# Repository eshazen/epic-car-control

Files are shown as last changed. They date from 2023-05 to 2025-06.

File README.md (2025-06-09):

# epic-car-control

Arduino-based model car control for EPIC.  This is a PCB which mounts
on a model car used in the Partner Classes taught at EPIC.

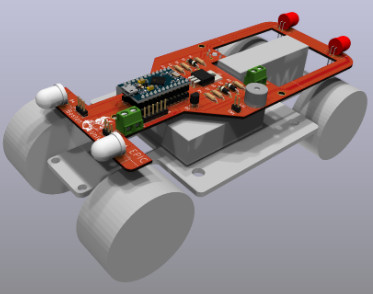
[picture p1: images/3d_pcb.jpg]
car


* [Electronics Talk](https://docs.google.com/presentation/d/1JKn2IykLU-F7YahLROMGz_joYOWPTk3rvR12y0UCeqs/edit?usp=drive_link) -- Google doc link for summer 2023 talk
* [Software Development Log](SoftwareLog.md)
* [Wiring Diagram](Slides/wiring_diagram.pdf) -- how to wire the PCB to the car
* [Programming Instructions](Slides/car_program.pdf) -- instructions to change the target distance

## Hardware features

* Arduino pro micro socket
* MOSFET for motor control
* Optical sensor for wheel revolution counter
* Headlights and taillights with individual control
* Small speaker
* Bottom-mounted pushbutton switch for user inputs
* Screw terminal connectors for a 6V battery pack (4xAA) and motor
* Header connector for a power switch

## Software

Current software in `Arduino/car_control/car_control.ino`

```
power-up reads distance set from EEPROM
   long (error) beep means invalid setting (default to 5)
Idle mode
   short press - drive for programmed distance
   long press - move to 10's set mode
10's set mode
   short press: add 10 revs
   long press: to 1's set mode
1's set mode
   short press: add 1 revs
   long press: save setting and exit to IDLE
```

Current setting displayed in binary on LEDs as

| Location | Value |
|:---|:---|
| Right Front | 1 |
| Left Front  | 2 |
| Left Rear | 4 |
| Right Rear  | 8 |

(value is sum of lit LEDs, or zero if all off)

Note that the current setting can be displayed with:

* **Long Press** - display 10's
* **Long Press** - display 1's
* **Long Press** - return to idle

Sensor test:

* Hold button while powering up
* Then press the button repeatedly:
  * first press: long beep, take reading, display low 4 bits
  * second press: display high 4 bits

Power down and up to exit test mode

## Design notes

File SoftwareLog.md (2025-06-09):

# Software log

**2025-06-08** Version 10

Another attempt to fix the EEPROM code.  Seems ok.
Programmed (40) boards for 2025 class.

**2025-06-03** Version 9

Still buggy EEPROM code

**2024-06-01** Version 8

Update sensor calibration values to 16 bit but bugs in EEPROM save so
doesn't restore correctly on power-up.

**2023-06-30** Working on sensor calibration

Created version 7.  Preliminary calibration mode.  Collects minimum
and maximum sensor readings and a threshold midway between them,
which is stored in EEPROM locations (2, 3).

Activate re-calibration by holding button down on power-up (replaces readout mode,
for now).  Spin front wheel until beeping stops.  Press button once
to go to normal driving mode.

A few other tweaks:  Ignore rotation sensor until running at speed.
I think it works well enough now.

**2023-06-29** First class

Deployed version 5.  All worked well on about half of the cars, but
the sensors didn't work well on the others.

**2023-06-19** Continuing on software.

The ISR stuff seems like a lot of work.  The debounce demo seems to
work fine with 20ms interrupts, so a main loop running at that speed
via delay() should be OK.  Here's the algo from the demo:

> Switch Debouncing uses high frequency hardware timer 50Hz == 20ms) to
> measure the time from the SW is pressed, debouncing time is 100ms =>
> SW is considered pressed if timer count is > 5, then call / flag SW is
> pressed When the SW is released, timer will count (debounce) until
> more than 50ms until consider SW is released.  We can set to flag or
> call a function whenever SW is pressed more than certain predetermined
> time, even before SW is released.

OK, first version is working ok.  Long/short button presses and rev
counter implemented using update() functions expected to be called
every ~20ms from loop().

**2023-06-18** Starting on working software.

Installed Arduino 2.1.0 as Appimage from the web.

`tone()` function works for beeping, and runs in background.

Idea:  use timer interrupts to record time/length of last button press.

Installing
[TimerInterrupt](https://github.com/khoih-prog/TimerInterrupt) v1.8.0
by Khoi Hoang, which claims to support the Leonardo.

This works OK but fights with tone(); Trying to create a unified ISR
which handles both, but the one with the button debounce demo seems to
take more than 1ms to run.

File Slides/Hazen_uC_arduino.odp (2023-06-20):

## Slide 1

EPIC Partner Class -- 2013

Soldering

and

Arduinos

## Soldering

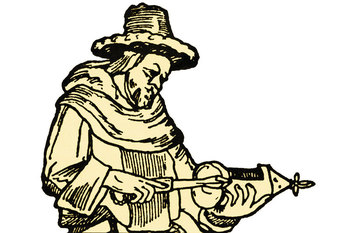
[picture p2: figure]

- Soldering is the joining of metal objects together. A filler metal (“solder”) is melted and flowed into the joint.
- Soldering was practiced in ancient Egypt at least 5000 years ago
- Soldering is used to attach electronic components to a board, and also for jewelery and other applications

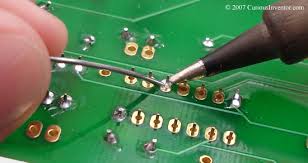
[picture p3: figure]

## Soldering Safety

- The iron gets hot! Don't burn yourself. Careful not to splash solder
- Solder is made of lead, which is poisonous Wash your hands when you are done; don't eat or drink while soldering
- Snipped component leads fly at high speeds Close your eyes or cover with your hands

## What's an Arduino?

A: A tiny computer

The black thing with all the legs

is a tiny computer called

a microcontroller

They can be programmed

in C or C++

They are used in lots of

things around your house

(microwave, stereo, TV...)

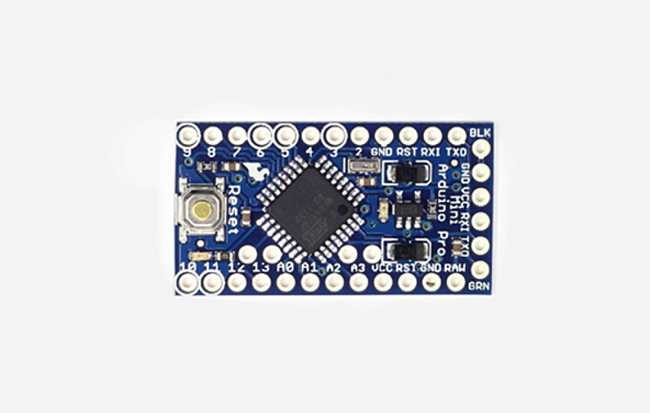
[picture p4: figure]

## Micro-what?

- Q: What exactly is a microcontroller (uC)? A: Just a very small (usually single-chip) computer
- Q: What features must a microcontroller have? A: A central processing unit (CPU) Program memory (usually flash) Data memory (at least registers, usually RAM too) Some input / output
- Q: What other features may a uC have? A: Counter/timer units, serial ports, A/D and D/A converters, plus sometimes special features such as USB, WiFi, light dimmers....

## Essential uC Components

Program Memory

Instructions (code)

Registers

(temporary storage)

Central

Processing

Unit

Input/

Output

External

Devices

Data Memory

(variables)

## Arduino “Sketch” Example It's almost exactly “C”, but...

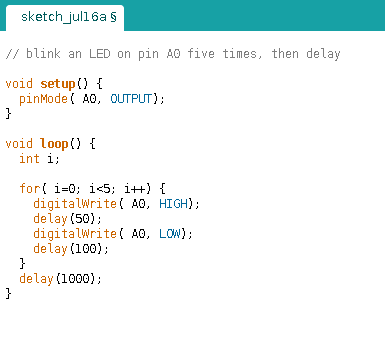
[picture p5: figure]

No “#includes” unless you use

a special library

Special function setup()
called once when program starts

pinMode() tells the Arduino
whether a pin is for input
our output

Special function loop()
called forever after setup()

DigitalWrite() sets a pin to
a specific “logic level”:
HIGH = 5V
LOW = 0V

No “printf” since there is no

keyboard / screen attached!

Special function delay()
stops the program for specified
number of milli-seconds
(1/1000 second steps)

## Circuit Example

Power supply

(two AA batteries)

Micro-

controller

LED

(output device)

resistor to limit

LED current

push-button

(input device)

## More about Input and Output

- Two types of devices:
  - Digital
    - On / Off only (like an LED or push-button)
    - Sometimes used in groups (i.e. for a keypad)
    - Can form a bus (special group with data and control) for example to control an LCD display
  - Analog
    - Variable level/speed (like a knob or a motor)
    - For input, use an ADC (analog-to-digital converter)
    - For output, use a DAC (digital-to-analog converter)
    - Often used for things like ultrasonic range finders, light sensors or speed control of motors

## Programming considerations

- Just like programming a “real computer”, except:
  - Generally C/C++ is the only language choice
  - Program memory is small! Programs must be short
  - Data memory is small! Only a few variables
  - Often there is no keyboard or display, so functions like printf() are not useful
  - Floating point math is “expensive” so best use only integers
  - For efficiency, pick variables of the right size (use a char if 8 bits is enough)

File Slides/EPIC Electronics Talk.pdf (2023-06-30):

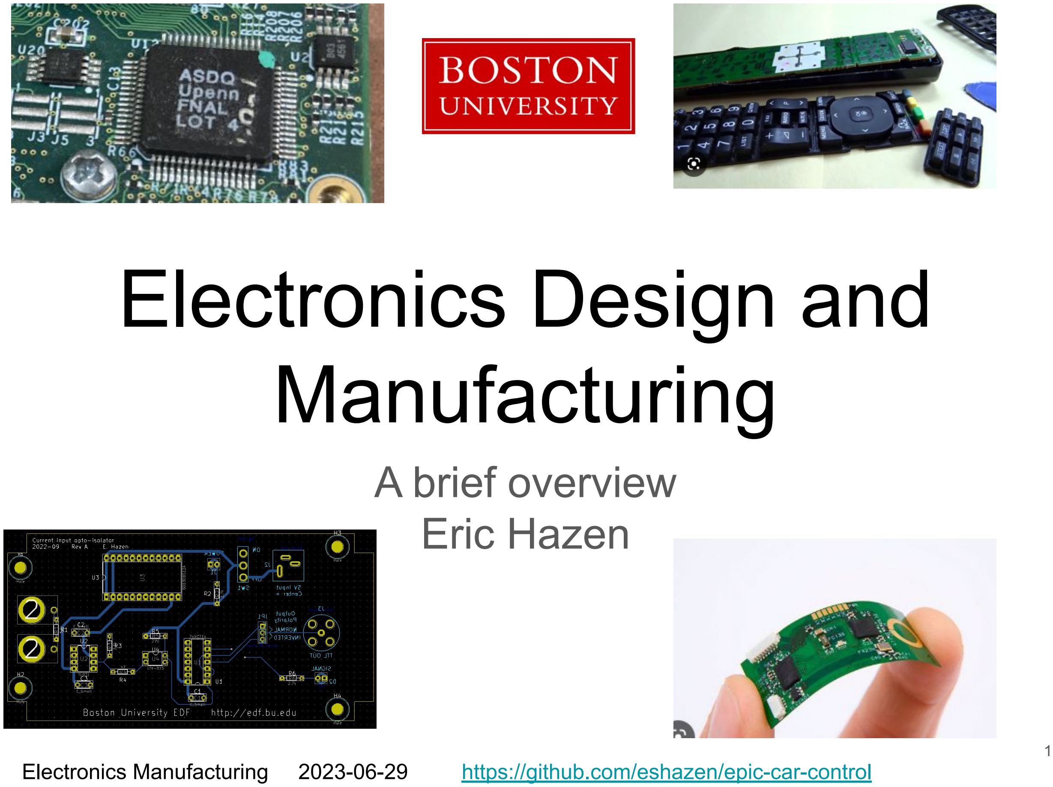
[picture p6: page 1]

# Electronics Design and Manufacturing

# A brief overview Eric Hazen

Electronics Manufacturing | 2023-06-29 | https://github.com/eshazen/epic-car-control

# About me…

Electronics Manufacturing | 2023-06-29 | E. Hazen | https://github.com/eshazen/epic-car-control

Professionally, I lead a team which built electronics for the CERN experiments which discovered the Higgs Boson
edf.bu.edu
(now retired)

In my spare time, I build
retro-electronics
(tube amps, calculators,
clocks…)

…and I fly planes and drive my Miata!

# Outline

## - Electronic Component types

## - Design Case Study

## - Packaging Considerations

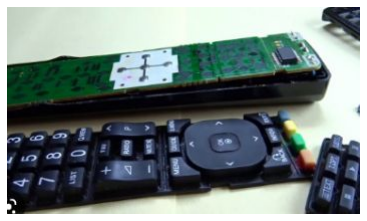
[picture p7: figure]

## - Power and Cooling

## - Summary

# Introduction to electronic components

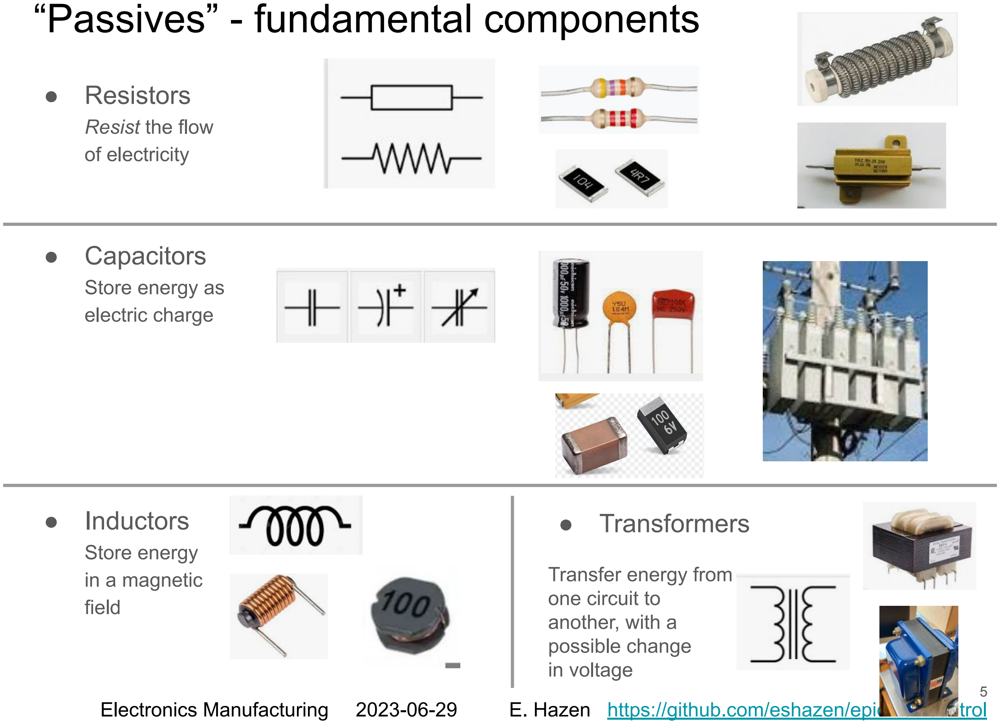
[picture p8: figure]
“Passives” - fundamental components; ● Resistors; Resist the flow of electricity; ● Capacitors; Store energy as electric charge; ● Inductors; Store energy in a magnetic field; ● Transformers; Transfer energy from one circuit to another, with a possible change in voltage

“Active” - Amplification and Switching; ● Transistors; Small current/voltage controls a larger current/voltage; ● Relays; Electromagnet controlled switch (power switching); ● Other Devices; Diode: rectification SCR/TRIAC for AC switching (dimmers, motor control); ● Vacuum Tubes; Predecessor to transistor Mostly obsolete, except Hobbyists and crazy Physicists!; BJT (bipolar junction); MOSFET; Many package options; DIODE

# Controls and Displays

## - Switches

## - Rotary / slide controls

Encoders provide digital Inputs. Potentiometers provide
variable resistance

## - LEDs

## - Displays

# Integrated Circuits (ICs, “chips”)

## Thousands/millions of components

integrated in a small area.

Etched on circular silicon wafers,

## Each containing hundreds of identical ICs

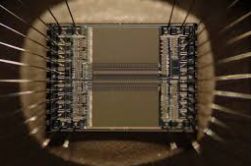
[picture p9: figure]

## Wafers are diced into individual die

## Wires are attached, and usually the dice are moulded in plastic packages suitable for

soldering.

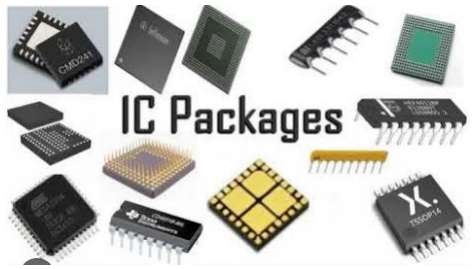
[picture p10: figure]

## Many factors must be considered when choosing a package, but usually the circuit designer has few choices (it is up to the IC

manufacturer).

# Connectors

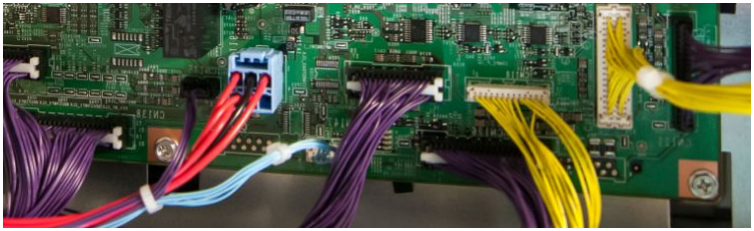
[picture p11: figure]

## - Connector types

- Power
- Low-speed signal
- High-speed signal
- Serial data (low wire/pin count)
- Parallel data (high wire/pin count)
- Radio Frequency (RF)
for antennas and such

## - Best to avoid them as much as possible!

Connectors and cables are often overlooked, but can add substantially to product cost

A connection on a PC board is “free” while connectors are expensive

# Case Study

# Model Car Electronics Design Process

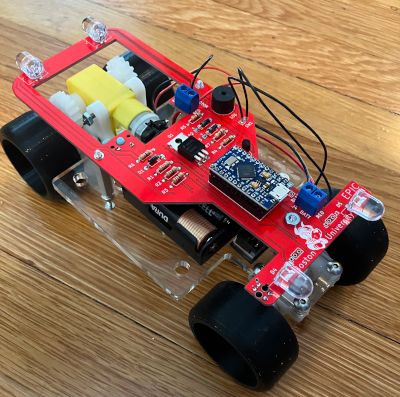
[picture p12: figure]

# Specifications

## Usually there is a written or verbal specification

## In this case…

## “This is a boring car, it needs some electronics!” :)

Or…

## “Provide motor control, lights, distance log and audible feedback with a programmable controller”

# Mechanical Considerations

Start with a simple CAD model of the mechanical part of the system.

# Mechanical Considerations

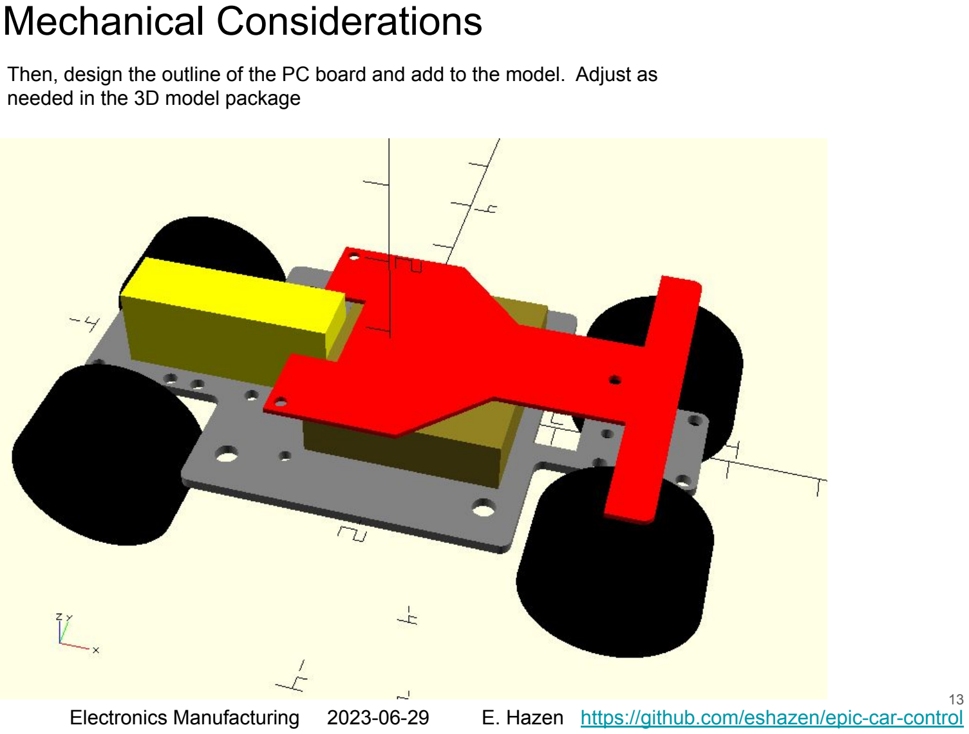
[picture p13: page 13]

Then, design the outline of the PC board and add to the model. Adjust as needed in the 3D model package

# Mechanical Considerations

It is recommended to make a mechanical mock-up of the electronics to be sure it fits. In this case I laser-cut a piece of acrylic the same dimensions as the PCB… it fits!

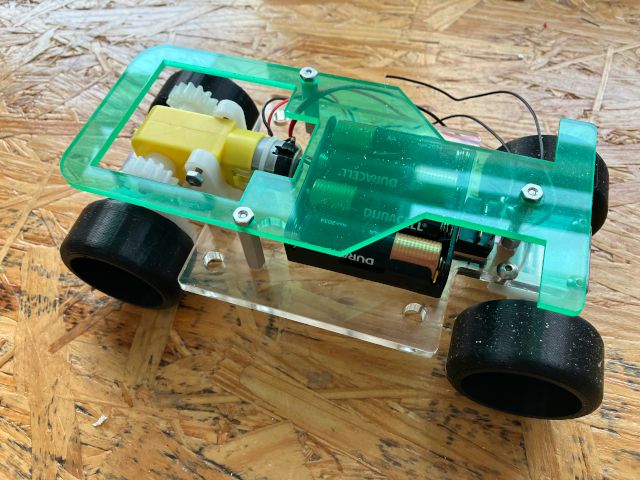
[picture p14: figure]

# Conceptual Design

## - Evaluate functionality (what does it have to do?)

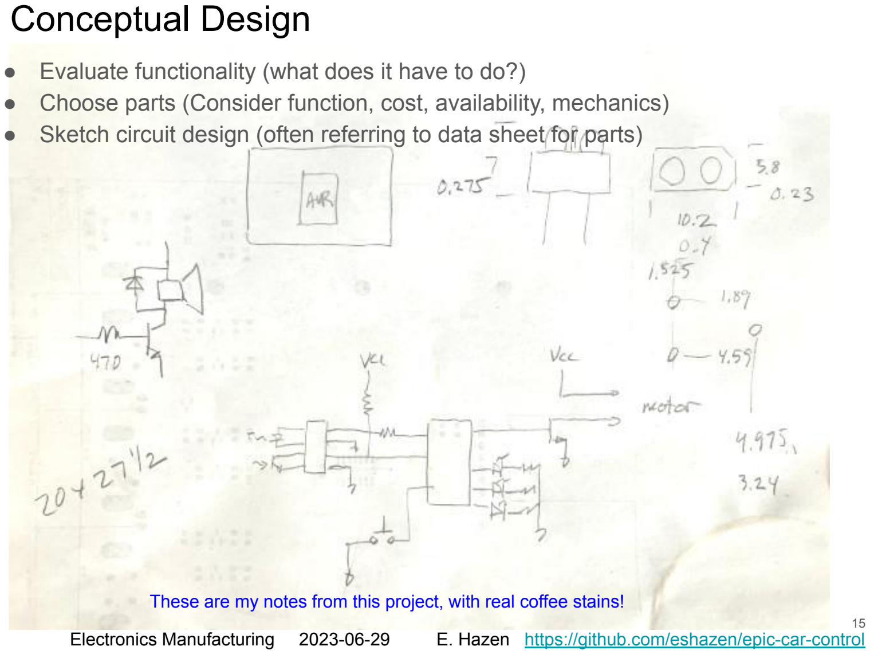
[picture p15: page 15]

## - Choose parts (Consider function, cost, availability, mechanics) - Sketch circuit design (often referring to data sheet for parts)

These are my notes from this project, with real coffee stains!

# Capture Electrical Schematic

## - Primarily for humans to read (though software can read it too…) - Shows the logical connections between parts (unrelated to the final physical layout) - Use “schematic capture” software (in this case, the free “KiCAD” schematic)

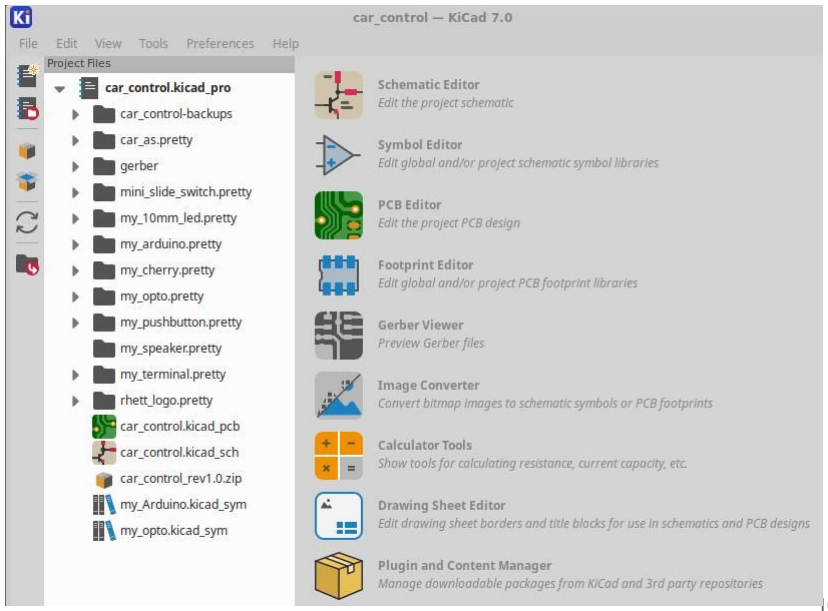
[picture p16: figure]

## Sales pitch:

KiCAD (www.kicad.org)
is a free, open-source
electronics design package which runs on all popular
OS (Mac, Windows, Linux)

We use it extensively

For more sophisticated projects we use proprietary tools
(Altium, Mentor, Cadence…)

# Schematic

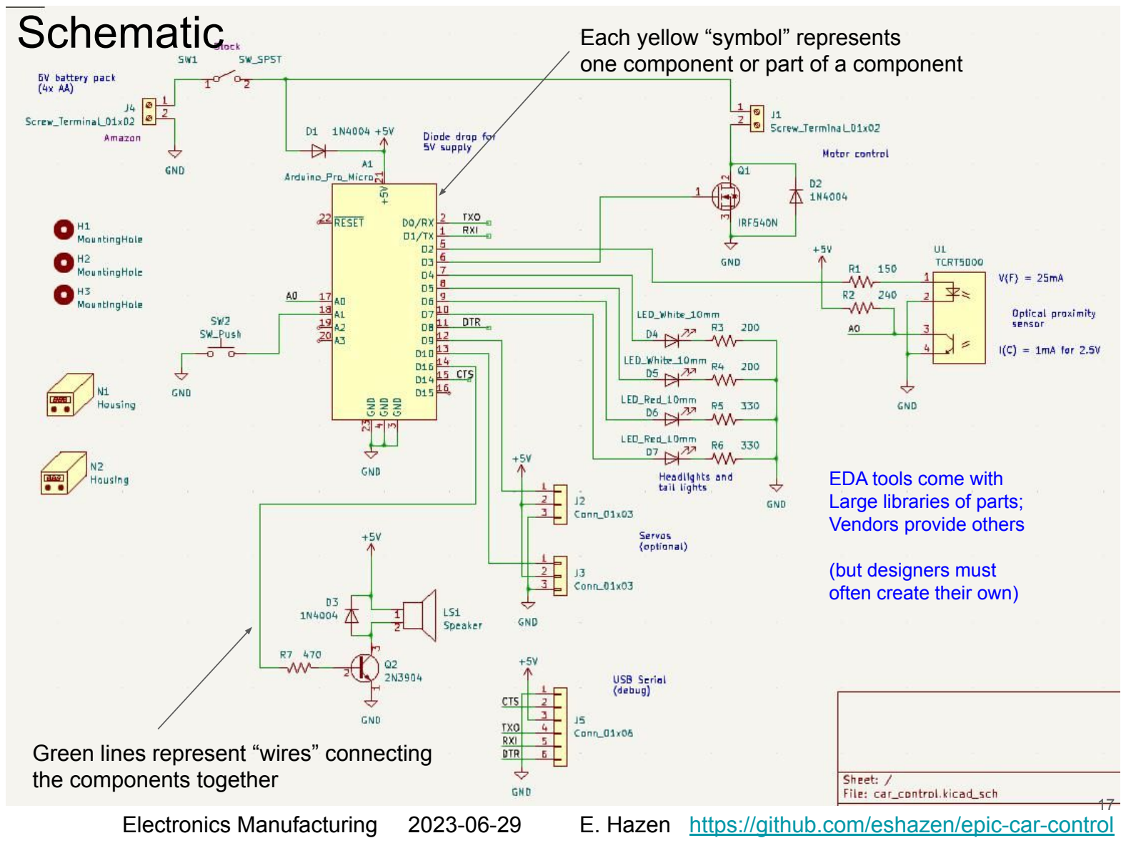
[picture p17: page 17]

Each yellow “symbol” represents
one component or part of a component

EDA tools come with
Large libraries of parts;
Vendors provide others

(but designers must
often create their own)

Green lines represent “wires” connecting the components together

# Physical Design (“Layout”)

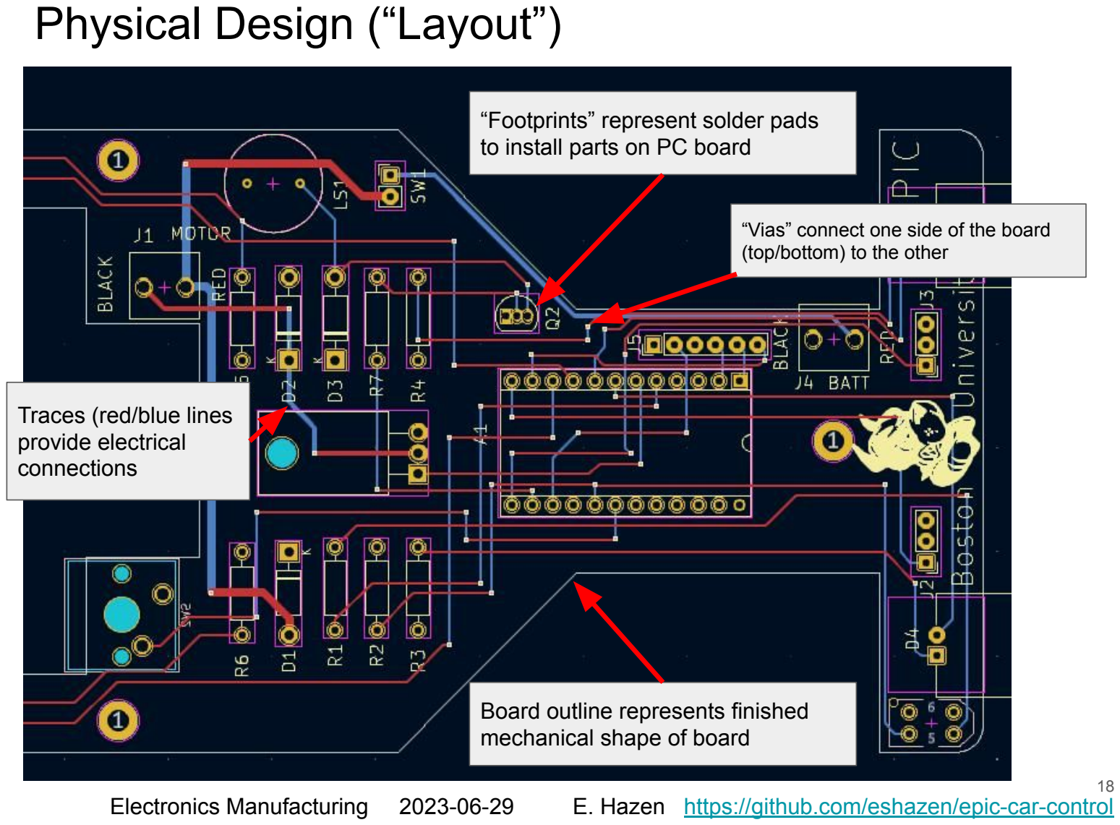
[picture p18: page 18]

“Footprints” represent solder pads to install parts on PC board

Traces (red/blue lines
provide electrical
connections

Board outline represents finished mechanical shape of board

“Vias” connect one side of the board (top/bottom) to the other

# Mechanical Considerations

## Export 3D model of completed PCB design and integrate with mechanical model Looks good! Let’s build it!

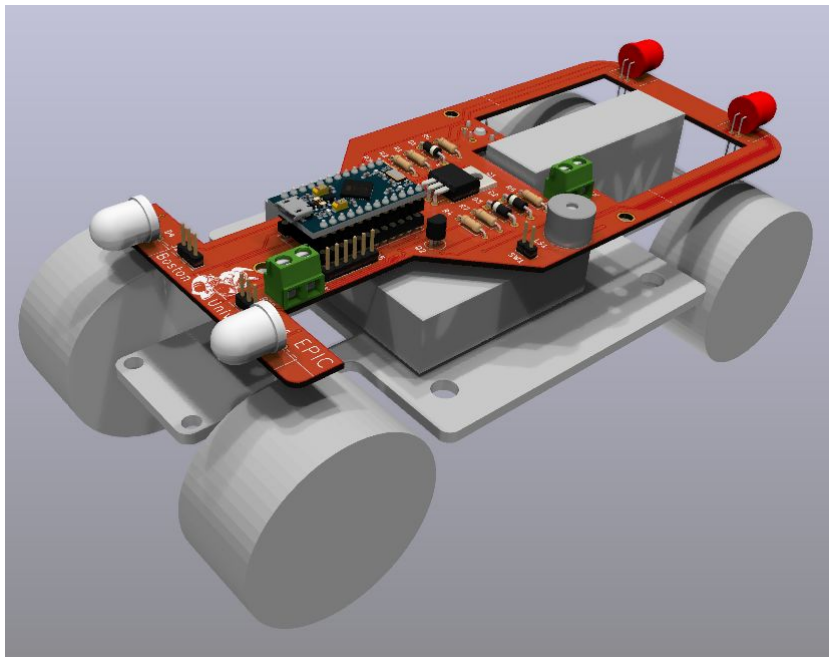
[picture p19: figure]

Electronic / Mechanical design tool integration is revolutionary!

# Bare PCB after fabrication

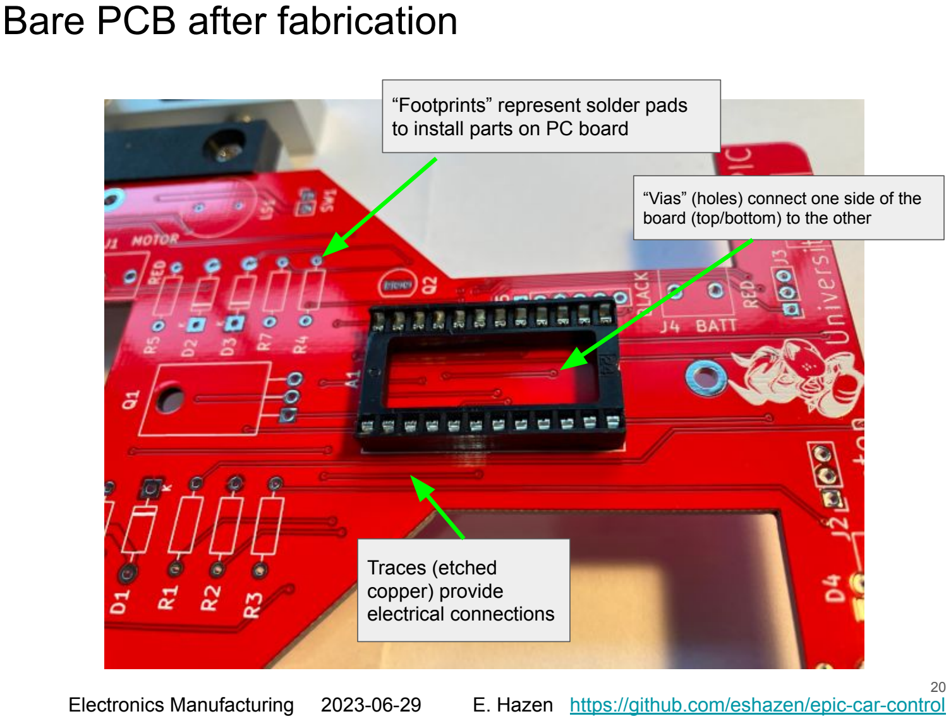
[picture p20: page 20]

“Footprints” represent solder pads to install parts on PC board

“Vias” (holes) connect one side of the board (top/bottom) to the other

Traces (etched
copper) provide
electrical connections

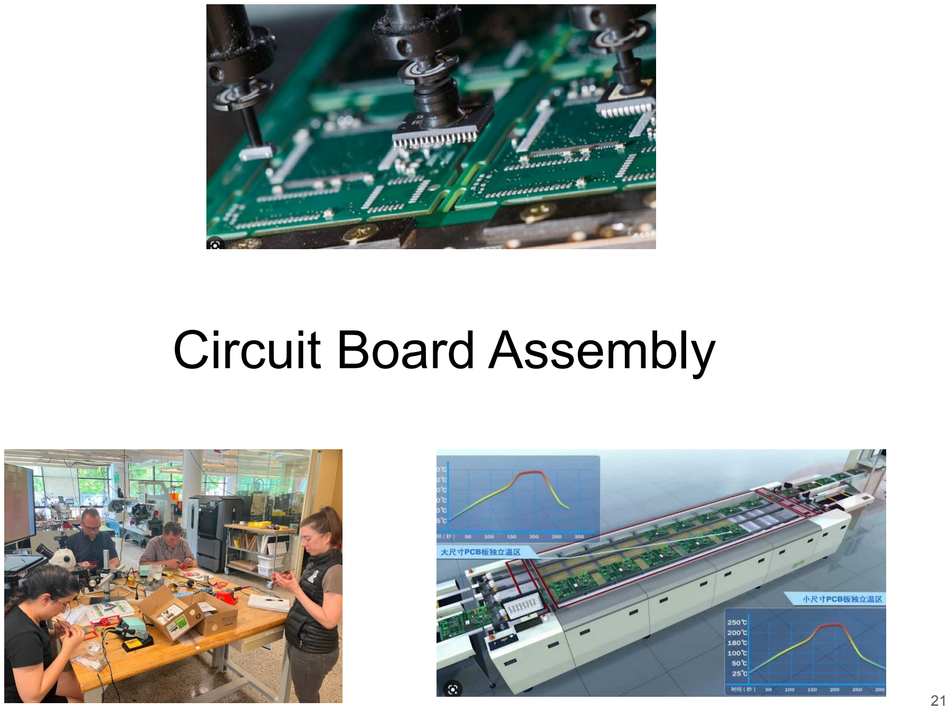
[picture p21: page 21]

# Circuit Board Assembly

# Component placement

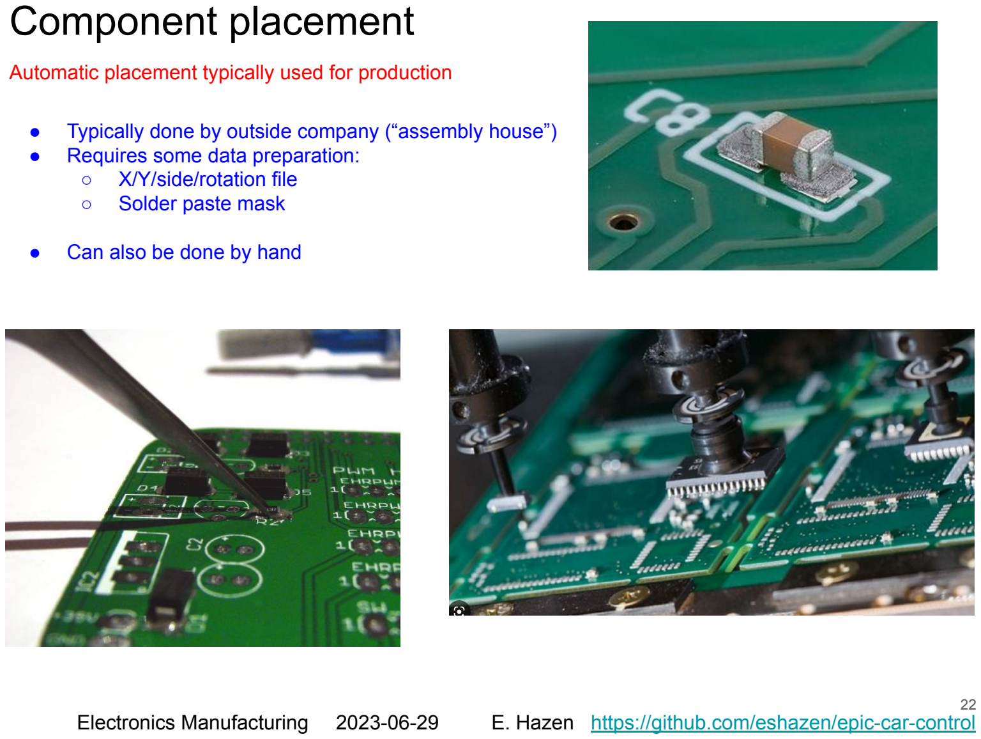
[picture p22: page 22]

- Typically done by outside company (“assembly house”)
- Requires some data preparation:
- X/Y/side/rotation file
- Solder paste mask
- Can also be done by hand

Automatic placement typically used for production

# Solder paste application

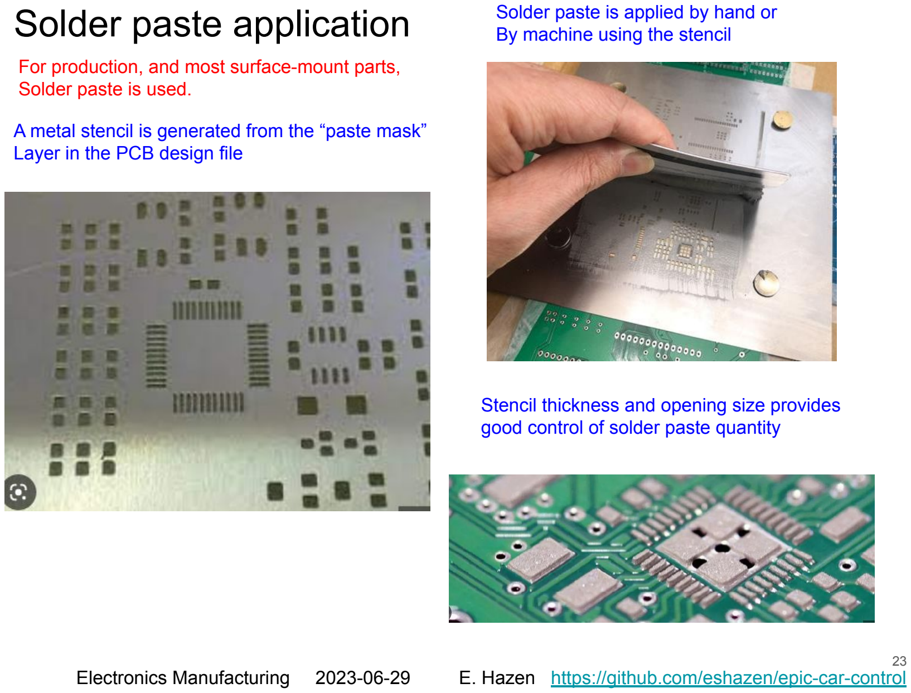
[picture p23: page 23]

A metal stencil is generated from the “paste mask” Layer in the PCB design file

Solder paste is applied by hand or By machine using the stencil

Stencil thickness and opening size provides good control of solder paste quantity

For production, and most surface-mount parts, Solder paste is used.

# Soldering

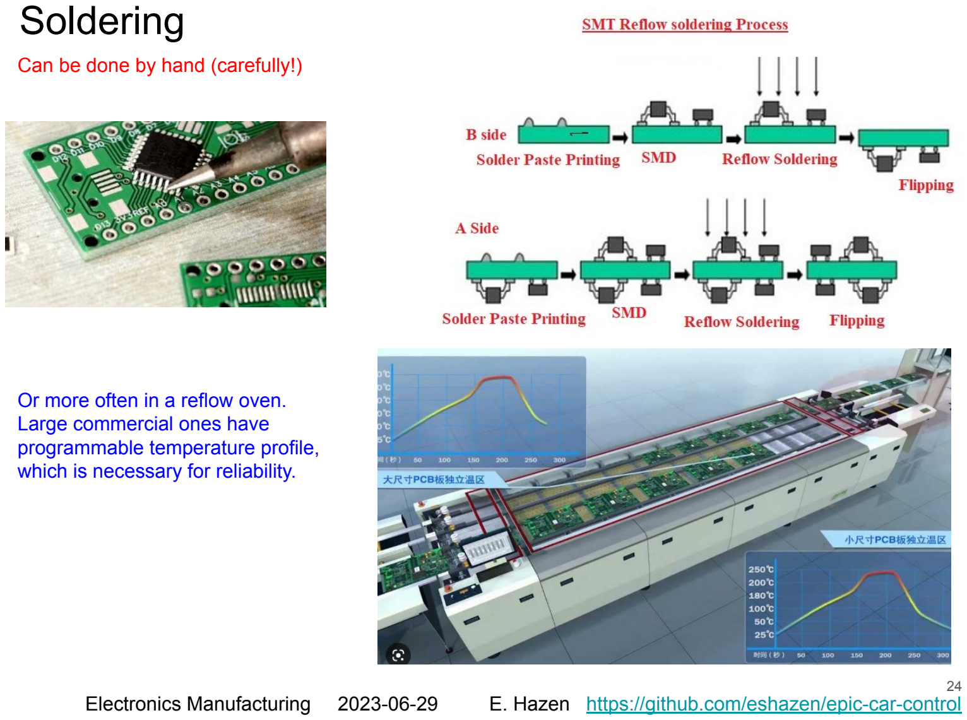
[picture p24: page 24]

Can be done by hand (carefully!)

Or more often in a reflow oven. Large commercial ones have programmable temperature profile, which is necessary for reliability.

# DIY soldering

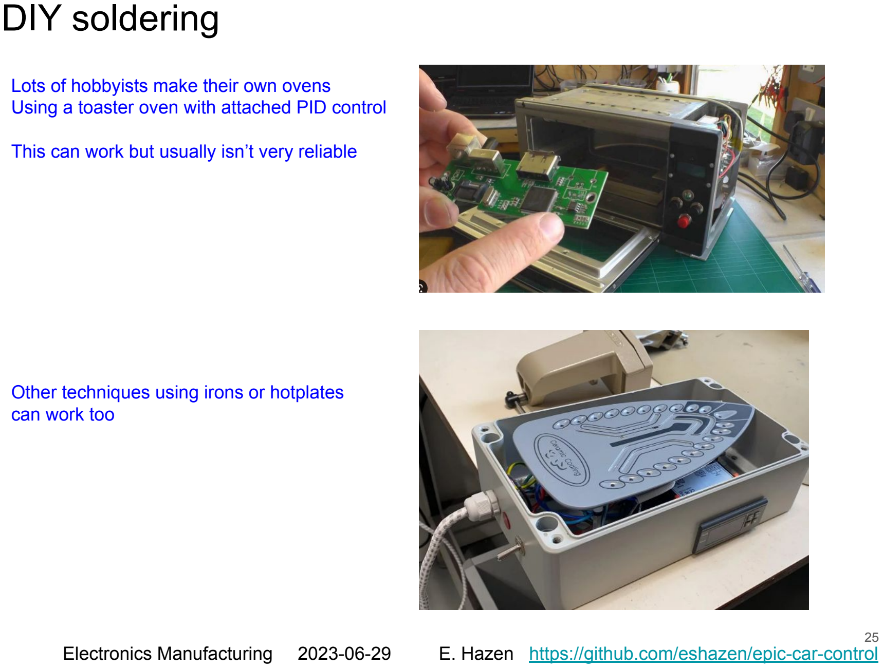
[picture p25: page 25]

Lots of hobbyists make their own ovens Using a toaster oven with attached PID control

This can work but usually isn’t very reliable

Other techniques using irons or hotplates can work too

# Assembling the Cars!

## It was a team effort! Next year maybe we’ll have you folks do some of it :)


# Packaging Considerations

## - Mechanical

## - Environmental

## - Interface

## - Power/Cooling

## PCBs need protection from vibration and significant shock to avoid broken connections

Electronics must be protected from moisture,

## heat, chemicals and even direct sunlight

## Controls, displays, connectors must be accessible while maintaining above protection

## All electronics produces heat. Power dissipation above a few mW must be considered in package design. Fans should be

avoided wherever possible.

# Packaging options

## - Moulded plastic case


- Board should be conformal coated to prevent moisture damage.
- Appropriate for consumer applications with low environmental stress
- DIfficult to moisture/weather proof
- Typically custom design/manufacture

## - Metal enclosure

- For industrial applications with high environmental stress
- Typically off-the-shelf enclosure with custom machining (though sometimes a full custom design)
- Relatively easy to waterproof

Packaging Options II; ● Chip-on-board (COB) Less expensive than traditional soldered packages for very large volume manufacturing; ● Flexible circuits Many applications:; ○ Portable electronics ○ Wearable electronics ○ Interconnections; Design similar to standard PCBs Still have to consider environmental protection; ● Potting / Encapsulation; Provides environmental protection (moisture, vibration); COB: Chip glued to PCB under “glob”; (vs traditional soldered package)

# Power

## - Power - essentially two choices:

- AC power
Best to avoid anything with AC inside the box (needs regulatory approval)

Use a “brick” or “wall wart” supply

- Battery power

Many types. Must consider:
■ | Suitability for use case (voltage/current)
■ | Replaceable vs rechargeable
■ | Charging options
■ | Gas emitted during charging
■ | Possibility of catastrophic failure
| (fire, explosion)
■ | User experience (battery life, charging time)
■ | Battery “fuel gauge”

Cooling; ● First, try to minimise power to simplify cooling! ● Cooling options; ○ Passive cooling (ambient air) ○ Active cooling; Forced air cooling (fan); Liquid cooling; Heat pump; ● When do I need active cooling?; ○ Typically < 1W total can be passive ○ Above this you have to engineer the cooling into the product; ● Additional considerations; ○ Ambient operating temperature range ○ Fans require power and make noise ○ Over-temperature shutdown to prevent damage or fire; Avoid this!; Heatsinks can improve both passive and active cooling; Fans can cool individual heat loads; Or the entire enclosure

Most power in electronics is dissipated as heat (except for some exceptions such as motors, lasers).

Summary; ● Consider the electronics from the start of the design process; ● Encourage the EE to minimise power and maximise mechanical robustness; ● Think about power and cooling very early, along with the user experience.; ● Build a mock-up or simulator to test ideas and validate simulation/estimates.

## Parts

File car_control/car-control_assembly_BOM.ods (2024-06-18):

Reference | Value | Qty
A1 | Arduino socket | 1
D1,D2,D3 | 1N4004 | 3
D4,D5 | LED_White_10mm | 2
D6,D7 | LED_Red_10mm | 2
J2,J3 | Conn_01x03 | 2
J5 | Conn_01x06 | 1
LS1 | Speaker | 1
Q1 | IRF540N | 1
Q2 | 2N3904 | 1
R1 | 150 | 1
R2 | 240 | 1
R3,R4 | 200 | 2
R5,R6 | 330 | 2
R7 | 470 | 1
SW1 | Conn_01x02 | 1
SW2 | SW_Push (bottom) | 1
U1 | TCRT5000 | 1

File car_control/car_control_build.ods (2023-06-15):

# | Reference | Qty | Value | Footprint | DNP | CatNo | Step
1 | A1 | 1 | Arduino_Pro_Micro | my_arduino:pro_micro_socket |  | Amazon (generic) | 1
2 | D1, D2, D3 | 3 | 1N4004 | Diode_THT:D_DO-41_SOD81_P10.16mm_Horizontal |  | Amazon (generic) | 2
3 | D4, D5 | 2 | LED_White_10mm | my_10mm_led:LED_D10.0mm_white |  | Amazon (generic) | 11
4 | D6, D7 | 2 | LED_Red_10mm | my_10mm_led:LED_D10.0mm_red |  | Amazon (generic) | 10
5 | H1, H2, H3 | 3 | MountingHole | MountingHole:MountingHole_2.7mm_M2.5_DIN965_Pad |  | DNP
6 | J1, J4 | 2 | Screw_Terminal_01x02 | my_terminal:Wuerth_WR-WTB_64800211622_1x02_P1.50mm_Vertical |  | Amazon | 9
7 | J2, J3 | 2 | Conn_01x03 | Connector_PinHeader_2.54mm:PinHeader_1x03_P2.54mm_Vertical |  | DNP
8 | J5 | 1 | Conn_01x06 | Connector_PinHeader_2.54mm:PinHeader_1x06_P2.54mm_Vertical |  | DNP
9 | LS1 | 1 | Speaker | my_terminal:speaker_d12mm_h8.5_p6.5 |  | Amazon | 6
10 | N1 | 1 | Housing | rhett_logo:rhett_logo |  | DNP :)
11 | N2 | 1 | Housing | car_as:car_as |  | DNP
12 | Q1 | 1 | IRF540N | Package_TO_SOT_THT:TO-220-3_Horizontal_TabDown |  | Amazon (generic) | 5
13 | Q2 | 1 | 2N3904 | Package_TO_SOT_THT:TO-92_Inline |  | Amazon | 4
14 | R1 | 1 | 150 | Resistor_THT:R_Axial_DIN0207_L6.3mm_D2.5mm_P10.16mm_Horizontal |  | EDF | 3
15 | R2 | 1 | 240 | Resistor_THT:R_Axial_DIN0207_L6.3mm_D2.5mm_P10.16mm_Horizontal |  | EDF | 3
16 | R3, R4 | 2 | 200 | Resistor_THT:R_Axial_DIN0207_L6.3mm_D2.5mm_P10.16mm_Horizontal |  | EDF | 3
17 | R5, R6 | 2 | 330 | Resistor_THT:R_Axial_DIN0207_L6.3mm_D2.5mm_P10.16mm_Horizontal |  | EDF | 3
18 | R7 | 1 | 470 | Resistor_THT:R_Axial_DIN0207_L6.3mm_D2.5mm_P10.16mm_Horizontal |  | EDF | 3
19 | SW1 | 1 | SW_SPST | Connector_PinHeader_2.54mm:PinHeader_1x02_P2.54mm_Vertical |  | Stock
20 | SW2 | 1 | SW_Push | my_cherry:SW_Cherry_MX_1.00u_PCB |  | Amazon | 7
21 | U1 | 1 | TCRT5000 | my_opto:TCRT5000 |  | Amazon | 8

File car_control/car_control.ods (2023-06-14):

 |  |  |  |  |  |  |  | Needed for
# | Reference | Qty | Qty Total | Value | Footprint | CatNo | Qty in stock | June | Jul, Aug | Notes
1 | A1 | 1 | 75 | Arduino_Pro_Micro | my_arduino:pro_micro_socket | Amazon (generic) | 6 | 19 | 69 | Any “Arduino Pro Micro 5V” should work.
 | A1-B | 1 | 75 | Socket | 24 pin DIP socket | Amazon (generic) | 25 | 0 | 50 | Generic 24 pin IC socket 0.6 inch
2 | D1, D2, D3 | 3 | 225 | 1N4004 | Diode_THT:D_DO-41_SOD81_P10.16mm_Horizontal | Amazon (generic) | 100 | -25 | 125 | Any 1N400x rectifier diode
3 | D4, D5 | 2 | 150 | LED_White_10mm | my_10mm_led:LED_D10.0mm_white | Amazon (generic) | 50 | 0 | 100 | Any 10mm white LED
4 | D6, D7 | 2 | 150 | LED_Red_10mm | my_10mm_led:LED_D10.0mm_red | Amazon (generic) | 50 | 0 | 100 | Any 10mm red LED
5 | H1, H2, H3 | 3 | 225 | MountingHole | MountingHole:MountingHole_2.7mm_M2.5_DIN965_Pad | DNP
6 | J1, J4 | 2 | 150 | Screw_Terminal_01x02 | my_terminal:Wuerth_WR-WTB_64800211622_1x02_P1.50mm_Vertical | Amazon | 60 | -10 | 90 | 2-position screw terminal 5.08mm spacing
7 | J2, J3 | 2 | 150 | Conn_01x03 | Connector_PinHeader_2.54mm:PinHeader_1x03_P2.54mm_Vertical | DNP
8 | J5 | 1 | 75 | Conn_01x06 | Connector_PinHeader_2.54mm:PinHeader_1x06_P2.54mm_Vertical | DNP
9 | LS1 | 1 | 75 | Speaker | my_terminal:speaker_d12mm_h8.5_p6.5 | Amazon | 50 | -25 | 25 | Amazon https://a.co/d/8MCAgkZ
10 | N1 | 1 | 75 | Housing | rhett_logo:rhett_logo | DNP
11 | N2 | 1 | 75 | Housing | car_as:car_as | DNP
12 | Q1 | 1 | 75 | IRF540N | Package_TO_SOT_THT:TO-220-3_Horizontal_TabDown | Amazon (generic) | 10 | 15 | 65 | Any IRF540 TO-220 N channel MOSFET
13 | Q2 | 1 | 75 | 2N3904 | Package_TO_SOT_THT:TO-92_Inline | Amazon | 100 | -75 | -25 | Any 2N3904 TO-92
14 | R1 | 1 | 75 | 150 | Resistor_THT:R_Axial_DIN0207_L6.3mm_D2.5mm_P10.16mm_Horizontal | EDF |  | 25 | 75 | Don’t need to order
15 | R2 | 1 | 75 | 240 | Resistor_THT:R_Axial_DIN0207_L6.3mm_D2.5mm_P10.16mm_Horizontal | EDF |  | 25 | 75 | Don’t need to order
16 | R3, R4 | 2 | 150 | 200 | Resistor_THT:R_Axial_DIN0207_L6.3mm_D2.5mm_P10.16mm_Horizontal | EDF |  | 50 | 150 | Don’t need to order
17 | R5, R6 | 2 | 150 | 330 | Resistor_THT:R_Axial_DIN0207_L6.3mm_D2.5mm_P10.16mm_Horizontal | EDF |  | 50 | 150 | Don’t need to order
18 | R7 | 1 | 75 | 470 | Resistor_THT:R_Axial_DIN0207_L6.3mm_D2.5mm_P10.16mm_Horizontal | EDF |  | 25 | 75 | Don’t need to order
19 | SW1 | 1 | 75 | SW_SPST | Connector_PinHeader_2.54mm:PinHeader_1x02_P2.54mm_Vertical | EDF |  | 25 | 75 | Don’t need to order
20 | SW2 | 1 | 75 | SW_Push | my_cherry:SW_Cherry_MX_1.00u_PCB | Amazon | 45 | -20 | 30 | Generic cherry-compatible keyswitch
21 | U1 | 1 | 75 | TCRT5000 | my_opto:TCRT5000 | Amazon | 30 | -5 | 45 | TCRT5000 opto sensor
 | Build Qty: | 75 | (total number of sets of parts for 60 cars plus spares)
 | June Qty: | 25
 | NOTES:
 | Qty is per board (i.e. per car)
 | “Qty in stock” is the number I already purchased and have in hand
 | “DNP” means “do not populate” so ignore these
 | “EDF” means I can grab these from the EDF (no cost)

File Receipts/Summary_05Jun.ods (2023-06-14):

Date | Description | Total
05/29/23 | 25 IC sockets; 20 photo sensors; 3 Arduino pro micro | $39.16
06/02/23 | 50 Red LEDs 10mm dia | $7.43
05/28/23 | 50 pcs electronics buzzer | $9.55
05/27/23 | 10 PCS RFP30N06 MOSFET; 10 photo sensors | $18.79
05/31/23 | (100) 2N3904; (6) screw term (45) kb switch (100) diodes (100) red LED | $42.72
05/27/23 | 3 Arduino pro mini | $20.18
05/31/23 | 50 White LEDs 10mm dia | $8.49
05/31/23 | JLCPCB qty 25 custom PC boards incl shipping | $72.63
 | Total (so far) | $218.95

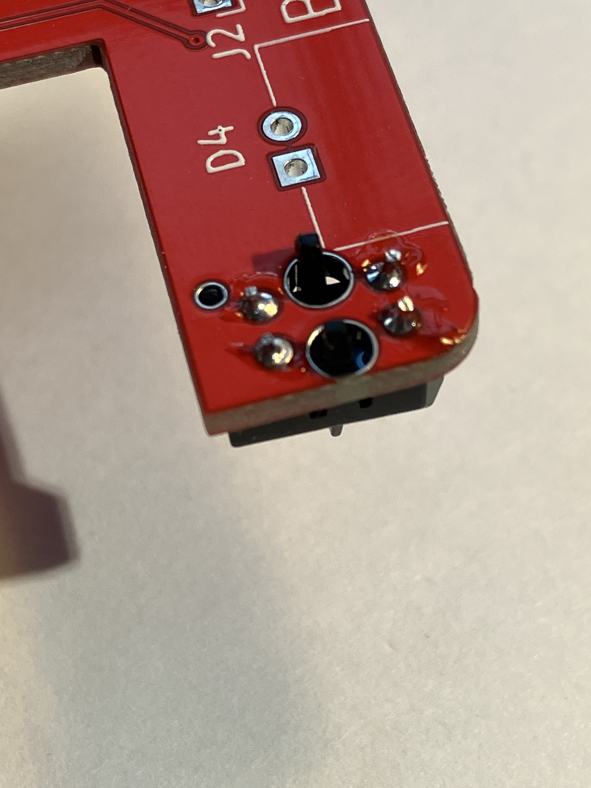
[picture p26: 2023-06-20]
parts_pix/2023-06-14 07.28.01.jpg

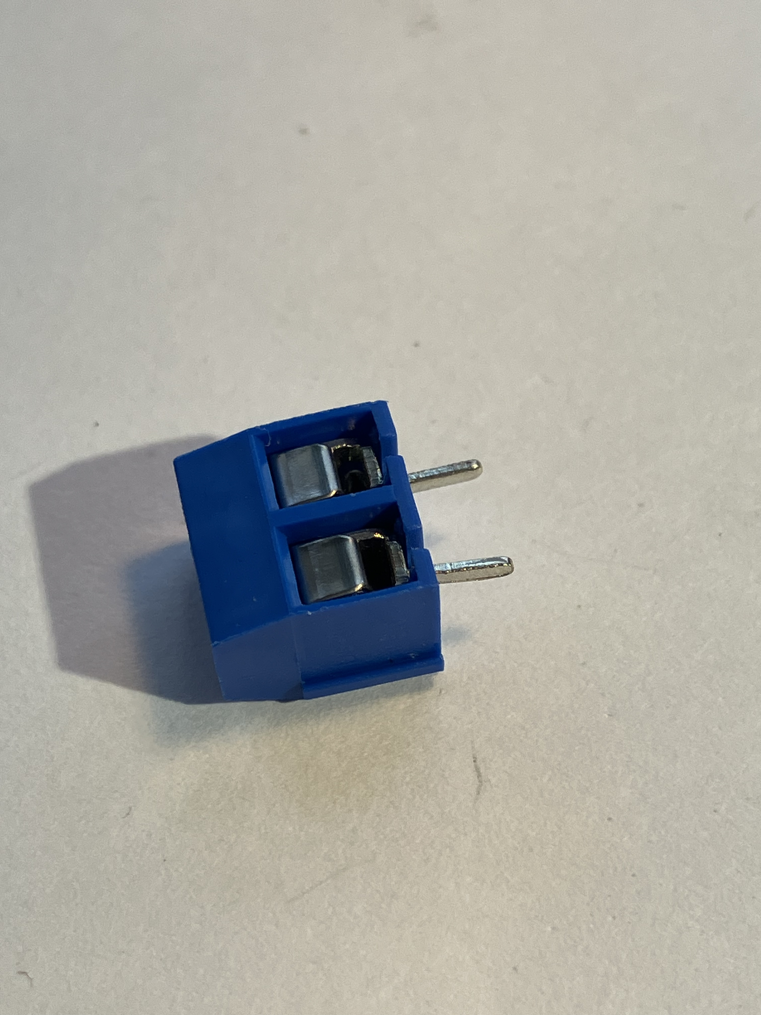
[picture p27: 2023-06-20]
parts_pix/2023-06-14 07.29.06.jpg

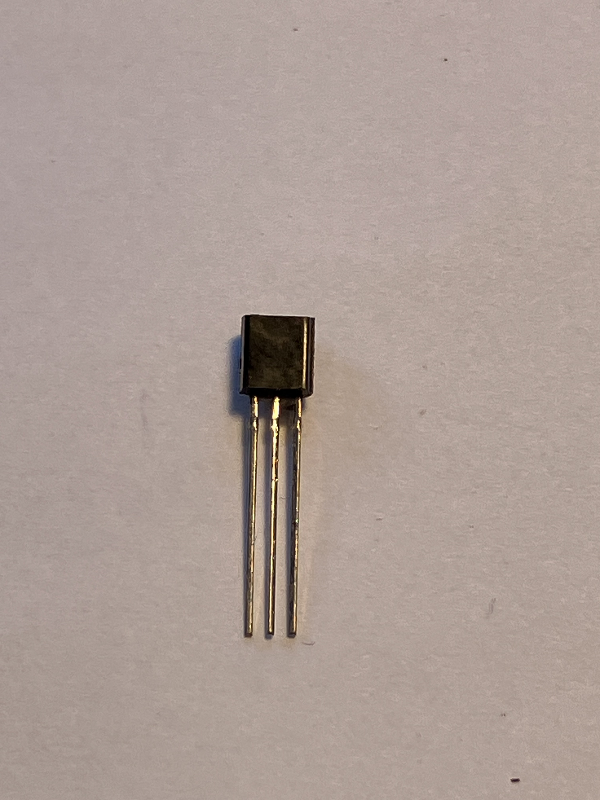
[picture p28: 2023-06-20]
parts_pix/2023-06-14 07.15.13.jpg

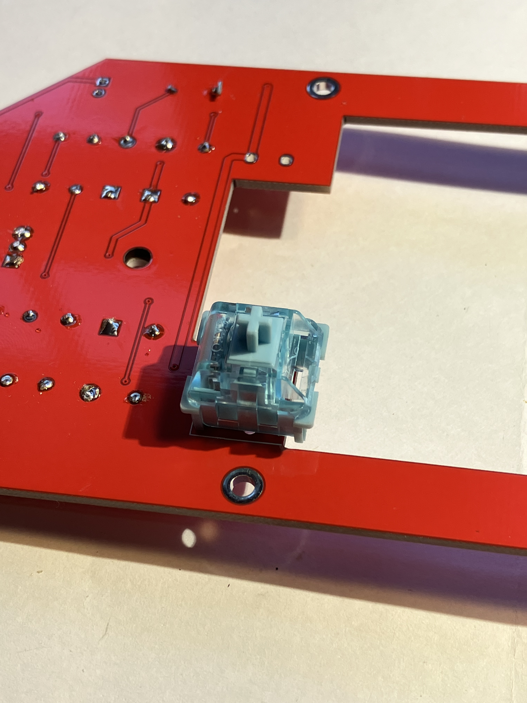
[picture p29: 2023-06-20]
parts_pix/2023-06-14 07.23.45.jpg

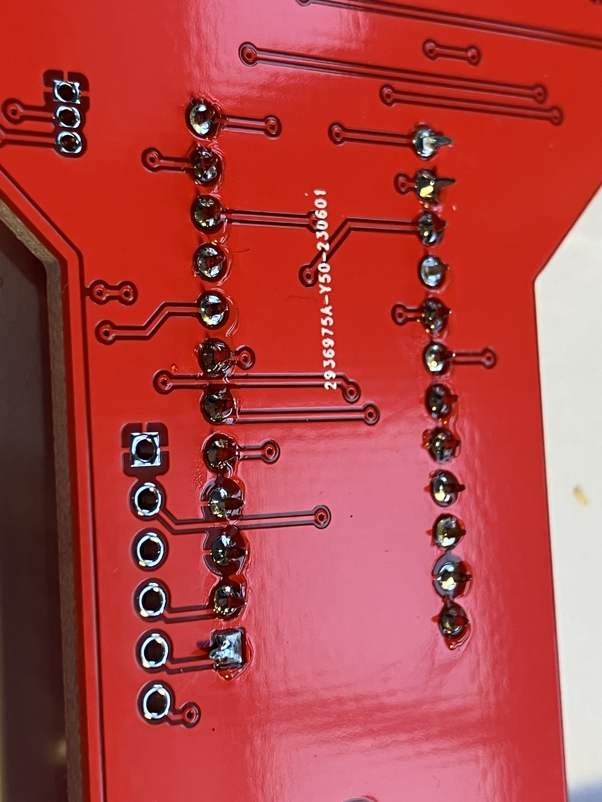
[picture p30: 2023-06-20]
parts_pix/2023-06-14 06.57.24.jpg

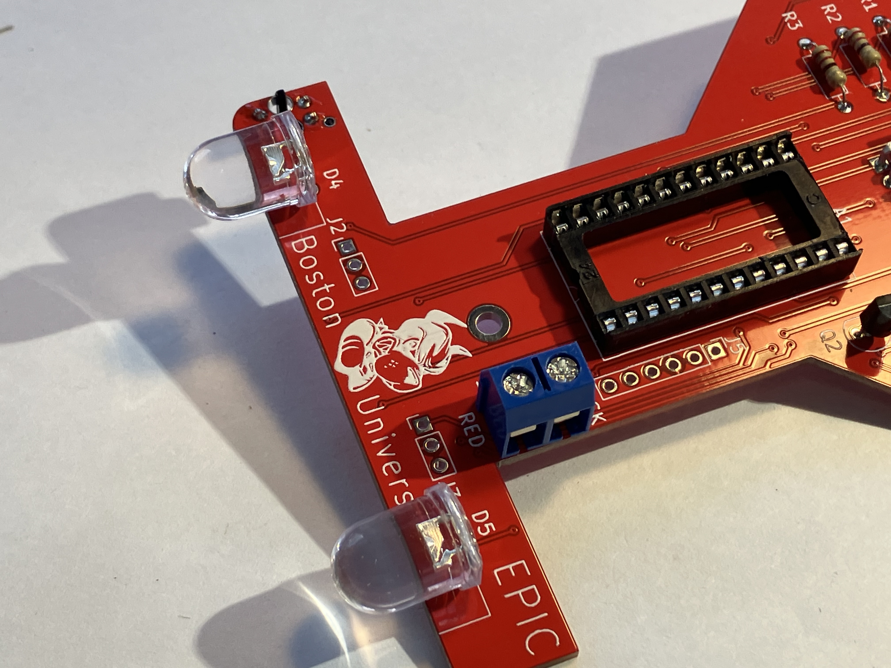
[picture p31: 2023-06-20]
parts_pix/2023-06-14 07.39.54.jpg

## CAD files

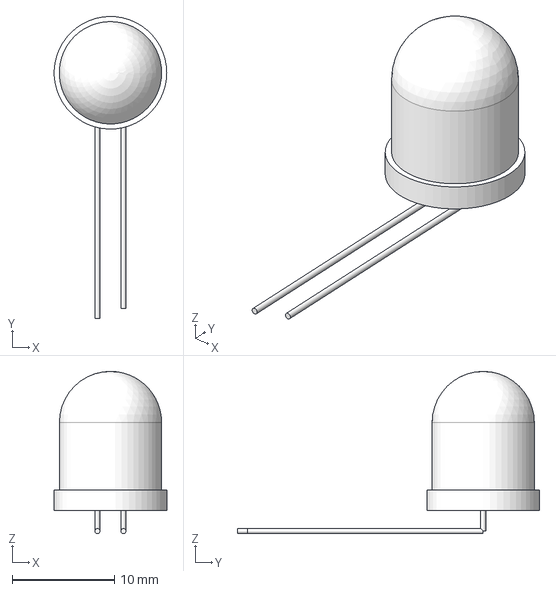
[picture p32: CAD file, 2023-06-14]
mech/led_10mm-White.step
11.0 x 29.5 x 15.8 mm

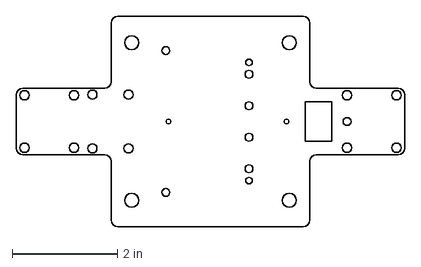
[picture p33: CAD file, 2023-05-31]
mech/temp/chassis_from_ohm.dxf
7.40 x 4.00 in

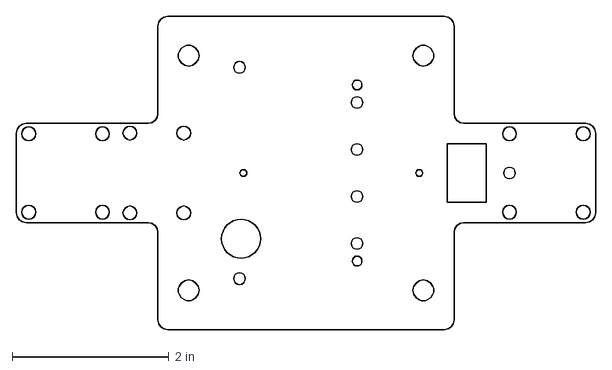
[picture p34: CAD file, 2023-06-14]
outbox/chassis_only.dxf
7.40 x 4.00 in

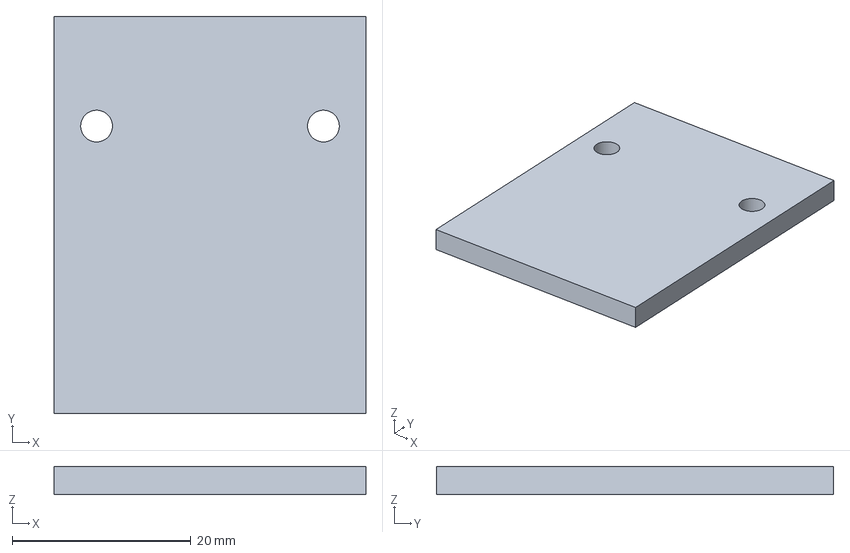
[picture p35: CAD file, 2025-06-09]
steering/chassis.3mf
34.9 x 44.5 x 3.18 mm

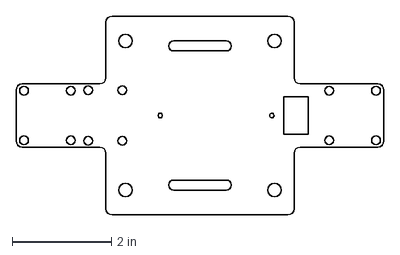
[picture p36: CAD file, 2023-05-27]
outbox/chassis_water_jet.DXF
7.40 x 4.00 in

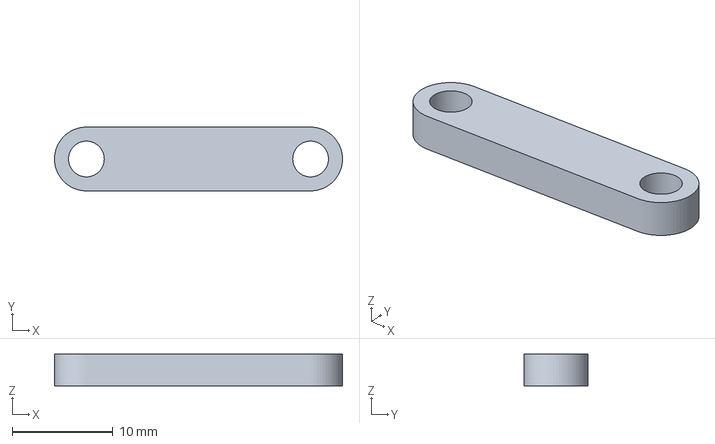
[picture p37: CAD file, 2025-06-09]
steering/crossbar.3mf
28.7 x 6.35 x 3.17 mm

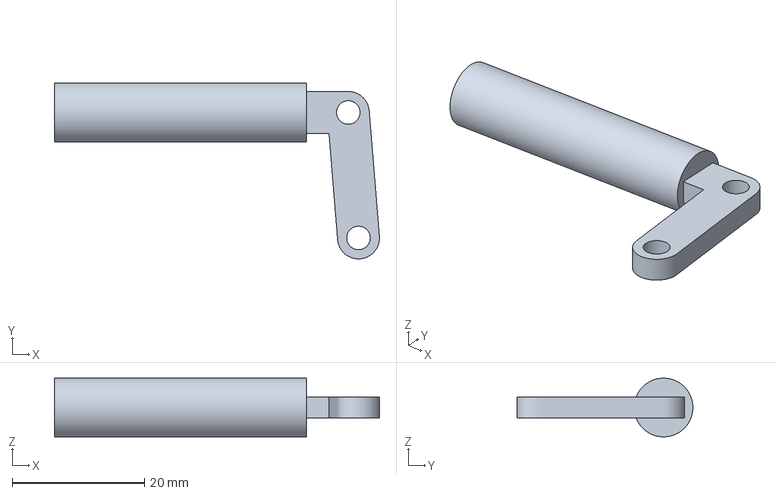
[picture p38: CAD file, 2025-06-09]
steering/bracket.3mf
49.2 x 26.6 x 8.89 mm

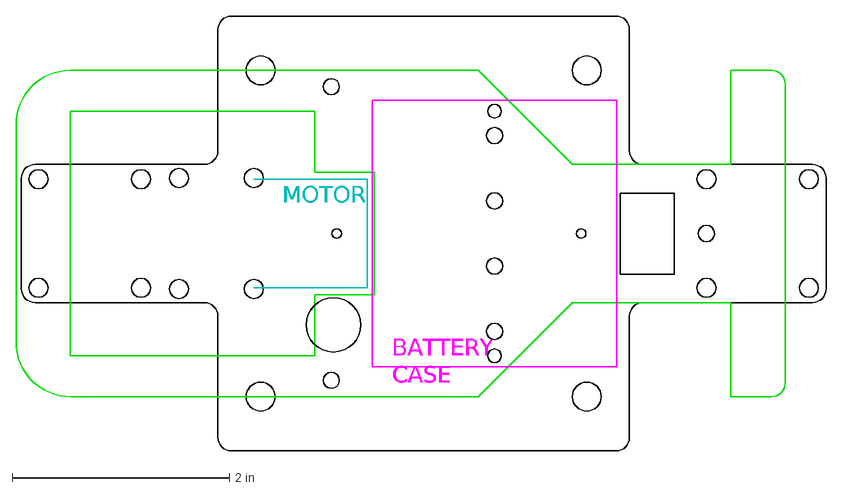
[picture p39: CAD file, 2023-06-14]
mech/modified_chassis.dxf
MOTOR
BATTERY CASE

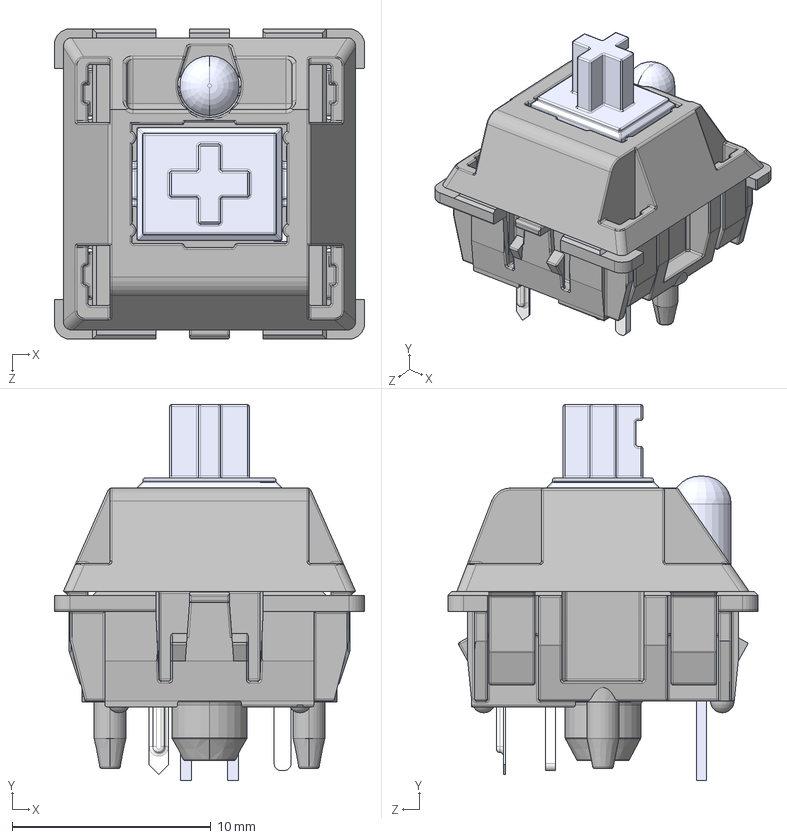
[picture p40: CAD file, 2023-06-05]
mech/cherry_mx.step
15.6 x 18.9 x 15.6 mm
MX 轴 按键′_ü___¨1
MX 轴 轴体áì_¨￠¨__
MX粣 拸簽LEDLEDLED
MX轴 轴体 底部 μ×2__默认_á2____è_
针脚___默认__è_

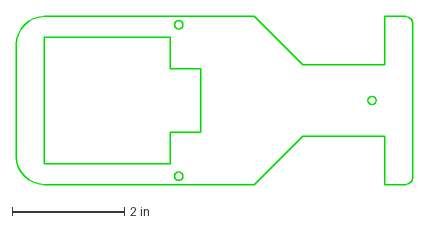
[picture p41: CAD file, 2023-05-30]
mech/board3.dxf
7.07 x 3.00 in

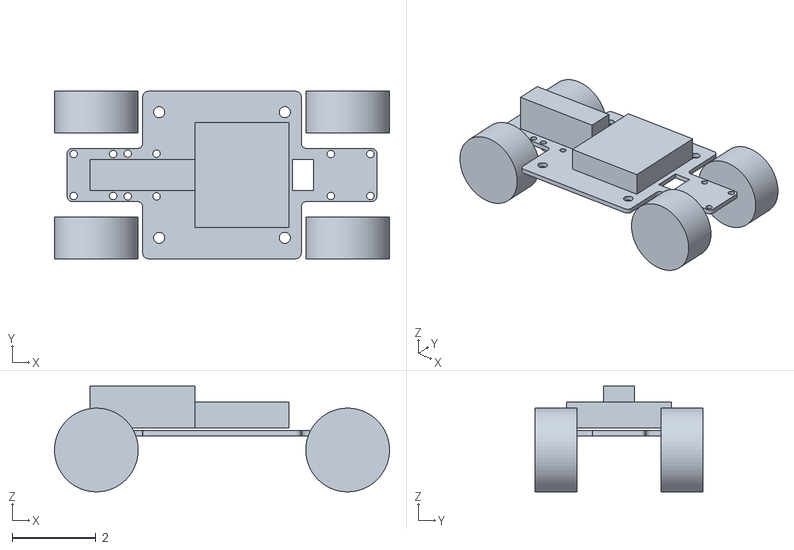
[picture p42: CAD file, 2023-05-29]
mech/car_as_footprint.stl
8.00 x 4.00 x 2.52

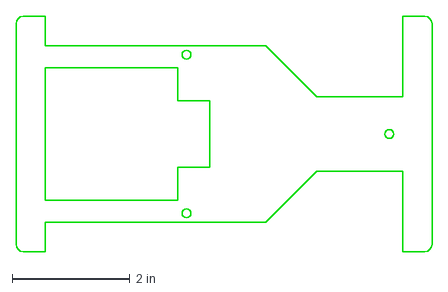
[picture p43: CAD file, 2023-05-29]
mech/board2.dxf
7.07 x 4.00 in

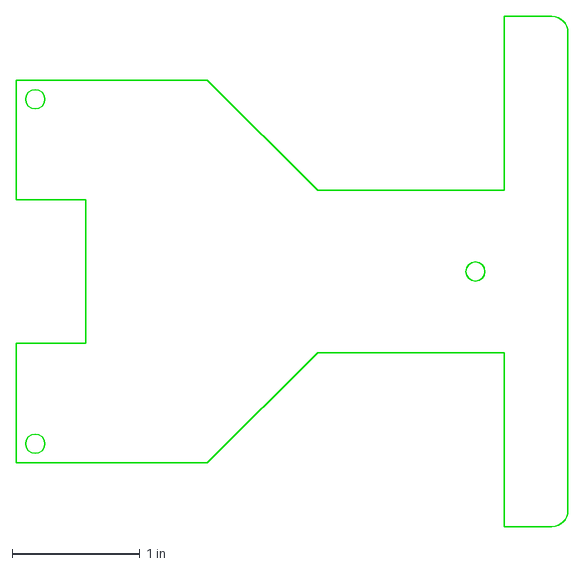
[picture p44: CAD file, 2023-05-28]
mech/board.dxf
4.33 x 4.00 in

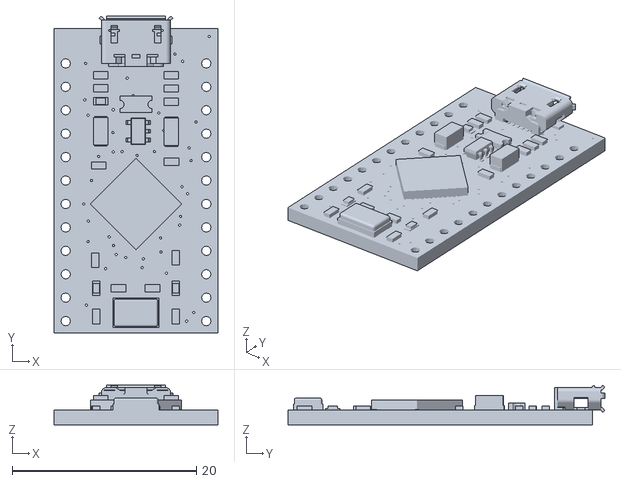
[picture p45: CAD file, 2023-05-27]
mech/Pro_Micro.stl
17.8 x 34.3 x 4.30

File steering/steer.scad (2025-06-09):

$fn = 64;
e = 0.1;
mm = 25.4;

show_wheels = 0;
show_brackets = 0;
show_chassis = 0;
show_both_sides = 0;
short_chassis = 0;
show_crossbar = 1;

pivot_hole = 0.14*mm;

// angle to steer
// steer_angle = ($t-0.5)*20;
steer_angle = 0;

// update to actual wheels
wheel_dia = 2.0*mm;
wheel_wid = 1*mm;
vehicle_wid = 4.0*mm;

wheelbase = 6.142*mm;

axle_dia = 0.35*mm;
axle_len = wheel_wid + 0.5*mm;

wheel_pivot_offset = 0.5*mm;

pivot_spc = vehicle_wid-2*wheel_wid-2*wheel_pivot_offset;
angle = atan2(wheelbase,pivot_spc/2);

bracket_stock_wid = 0.25*mm;
bracket_arm_len = 0.75*mm;
bracket_stock_thk = 0.125*mm;

// reference point where differential would be
//color("red") cylinder( h=30, d=1);

chassis_len = 7.5*mm;
chassis_thk = 0.125*mm;
chassis_tab_wid = 1.375*mm;
chassis_tab_len = 1.75*mm;

w = vehicle_wid;
l = chassis_len;
b = chassis_tab_len;
d = chassis_tab_wid;
a = (vehicle_wid-chassis_tab_wid)/2;
c = l-2*b;
pts_s = [ [0, b+c], [a, b+c], [a, l], [a+d, l], [a+d, l-b],
	  [0, b+c ]];
pts_l = [ [a, 0], [a, b], [0, b], [0, b+c], [a, b+c], [a, l],
	  [a+d, l], [a+d, l-b], [w, l-b], [w, b], [w-a, b],
	  [w-a, 0], [a, 0]];

module chassis() {
     if( short_chassis) 
	  linear_extrude( height=chassis_thk) polygon( points = pts_s);
     else
	  linear_extrude( height=chassis_thk) polygon( points = pts_l);
}

module crossbar() {
  // calculate endpoints of steering bar
  // left wheel
  left_x = wheel_pivot_offset-(vehicle_wid/2-wheel_wid) +
     cos(angle-steer_angle) * bracket_arm_len;
  left_y = wheelbase - sin(angle) * bracket_arm_len;
  left_z = 0;

  // right wheel
  right_x = -(wheel_pivot_offset-(vehicle_wid/2-wheel_wid) +
	      cos(angle+steer_angle) * bracket_arm_len);
  right_y = wheelbase - sin(angle) * bracket_arm_len;
  right_z = 0;

  crossbar_len = right_x - left_x;


  // draw the crossbar
  difference() {
       translate( [left_x, left_y, left_z+bracket_stock_thk]) {
	    // rounded ends
	    cylinder( d=bracket_stock_wid, h=bracket_stock_thk);
	    translate( [crossbar_len, 0, 0])
		 cylinder( d=bracket_stock_wid, h=bracket_stock_thk);
	    translate( [0, -bracket_stock_wid/2, 0])
		 cube( [crossbar_len, bracket_stock_wid, bracket_stock_thk]);
       }
       // indicate the pivot points
       translate( [left_x, left_y, -10]) cylinder( d=pivot_hole, h=20);
       translate( [right_x, right_y, -10]) cylinder( d=pivot_hole, h=20);
  }
       
}

// create a steering bracket
module bracket() {

     translate( [-wheel_pivot_offset, -bracket_stock_wid/2, 0])
	  cube( [wheel_pivot_offset, bracket_stock_wid, bracket_stock_thk]);

     rotate( [0, 0, -angle]) {
       translate( [0, -bracket_stock_wid/2, 0]) {
	    difference() {
		 union() {
		      cube( [bracket_arm_len, bracket_stock_wid, bracket_stock_thk]);
		      translate( [bracket_arm_len, bracket_stock_wid/2, 0])
			   cylinder( h=bracket_stock_thk, d=bracket_stock_wid);
		 }
		 translate( [bracket_arm_len, bracket_stock_wid/2, -1])
		      cylinder( d=pivot_hole, h=10);
	    }
       }
     }
     cylinder( h=bracket_stock_thk, d=bracket_stock_wid);
}


module wheel_at( x, y, z, steer) {
  translate( [ x+wheel_pivot_offset, y, z]) {
    rotate( [0, 0, steer]) {
      translate( [-wheel_pivot_offset, 0, 0]) {
	rotate( [0, 270, 0]) {
	     if( show_wheels) {
	     % cylinder( d=wheel_dia, h=wheel_wid);
		  translate( [0, 0, -(axle_len-wheel_wid)/2])
		       color("green") cylinder( d=axle_dia, h=axle_len);
	     }
	}
	// bracket with steering pivot
	if( show_brackets)
	translate( [wheel_pivot_offset, 0, -bracket_stock_thk/2]) {
	     difference() {
		  bracket();
		  translate( [0, 0, -1])
		       cylinder( d=pivot_hole, h=10);
	     }
	}
      }
    }
  }
}

// left front wheel
wheel_at( -(vehicle_wid/2-wheel_wid), wheelbase, 0, steer_angle);
// right front wheel
if( show_both_sides)
     mirror( [1, 0 ,0]) wheel_at( -(vehicle_wid/2-wheel_wid), wheelbase, 0, -steer_angle);

if( show_crossbar) crossbar();
if( show_chassis) {
     difference() {
	  translate( [-vehicle_wid/2, -chassis_tab_len/2, -5]) color("green") chassis();
	  translate( [-(vehicle_wid/2-wheel_wid)+wheel_pivot_offset, wheelbase, -10]) cylinder( d=pivot_hole, h=20);
	  mirror( [1, 0 ,0]) translate( [wheel_pivot_offset-(vehicle_wid/2-wheel_wid), wheelbase, -10]) cylinder( d=pivot_hole, h=20);
     }
}

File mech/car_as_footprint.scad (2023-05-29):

$fn=64;

chassis_z = 0.125;

module chassis() {
     color("gray")
     linear_extrude( height=chassis_z, center=true, convexity=10) {
	  import("modified_chassis.dxf", layer="0");
     }
}

module wheel() {
     color("black")
	  cylinder( h=1, d=2);
}     

wheel_z = -0.4;

module wheels() {
     rotate( [90, 0, 0]) {
	  translate( [3, wheel_z, 1]) wheel();
	  translate( [3, wheel_z, -2]) wheel();
	  translate( [-3, wheel_z, 1]) wheel();
	  translate( [-3, wheel_z, -2]) wheel();
     }
}

mot_x = 2.5;
mot_y = 0.75;
mot_z = 1;

chassis_x = 7.4;

module motor() {
     translate( [(-chassis_x/2)+0.55, -mot_y/2, chassis_z])
	  color("yellow")
	  cube([mot_x, mot_y, mot_z]);
}

batt_x = 2.25;
batt_y = 2.50;
batt_z = 0.625;

module battery() {
     translate( [(-chassis_x/2)+0.55+mot_x, -batt_y/2, chassis_z])
	  color("#908020")
	  cube( [batt_x, batt_y, batt_z]);
}


module opto() {
     scale( [0.0394, 0.0394, 0.0394])
	  color("#800080")
	  import("TCRT5000.stl");
}


pcb_above_batt = 0.125;

// module pcb() {
//      translate( [0, 0, chassis_z+batt_z+pcb_above_batt]) {
// 	  // PCB outline from DXF
// 	  color("red")
// 	       linear_extrude( height=0.063, center=true, convexity=10) {
// 	       import("modified_chassis.dxf", layer="PCB");
// 	  }
// 	  // imported arduino from STL
// 	  color("cyan")
// 	       translate( [2, -0.35, 0.2])
// 	       rotate( [0, 0, 90])
// 	       scale( [0.0394, 0.0394, 0.0394])
// 	       import("Pro_Micro.stl");
// 	  //
// 	  rotate( [270, 0, 0])
// 	  translate( [3, 0, 1.4])
// 	  opto();
//      }
// }


chassis();
wheels();
motor();
battery();
// pcb();

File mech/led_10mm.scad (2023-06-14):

//
// generic 10mm LED
//

$fn = 64;

dia = 10.0;
rad = 5;
hgt = 11.6-rad;
base_z = 2.0;
base_dia = 11;

pin_d = 0.5;
pin_z = 25;
pin_s = 2.54;

// bend pin at this Z
pin_b = 2;

module pin_at( x, y, ra, pl) {
  if( ra == 1) {
    // right-angle
    translate( [x, y, -pin_b]) {
      cylinder( d=pin_d, h=pin_b);
      rotate( [90, 0, 0])
	cylinder( d=pin_d, h=pl-pin_b);
    }
  } else {
    // vertical
    translate( [x, y, -pl])
      cylinder( d=pin_d, h=pin_z);
  }
}

module led( colr, ra) {
  color("gold") {
    pin_at( -2.54/2, 0, ra, pin_z+1);
    pin_at( 2.54/2, 0, ra, pin_z);
  }
  color( colr) {
    cylinder( h=base_z, d=base_dia);
    translate( [0, 0, base_z])
      cylinder( d=dia, h=hgt);
    translate( [0, 0, base_z+hgt])
      sphere( d=dia);
  }
}

// white
led( [1, 1, 1, 0.75], 1);
// red
// led( [1, 0, 0, 0.75], 1);

  

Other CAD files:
mech/led_10mm-Group.step
mech/led_10mm-red.step
mech/TCRT5000.stp
mech/pushbutton.scad
car_control/test.scad
mech/TCRT5000.stl
mech/simple_car.scad
mech/speaker.scad
mech/switch.scad

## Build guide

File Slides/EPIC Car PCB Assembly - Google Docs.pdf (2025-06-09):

EPIC Car PC Board Assembly | Rev 2025-06-02

### 1. A1 - Arduino socket

Mount with notch matching PCB

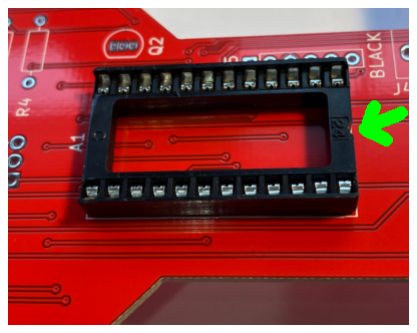
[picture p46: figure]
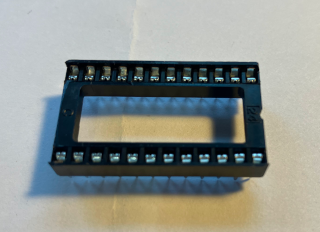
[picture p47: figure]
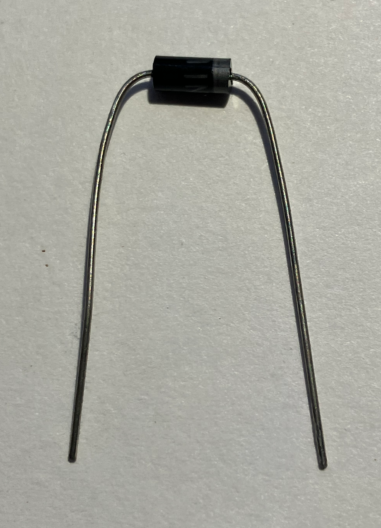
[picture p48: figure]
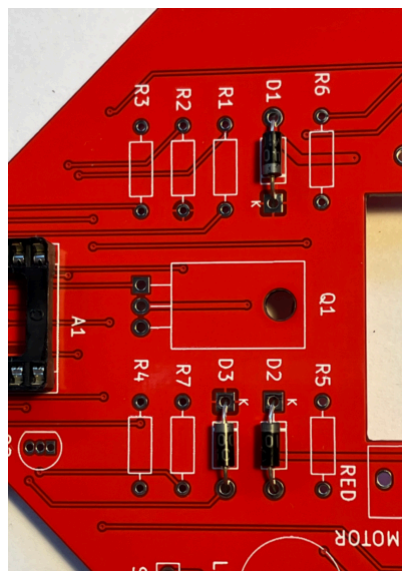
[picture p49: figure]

### 2. D1, D2, D3 - 1N4004 diodes

Bend leads as shown, Mount with band matching PCB

### 3. R1-R7 -- Resistors

Check color code! (or measure with meter)

R1 | - 120 ohms - Brown, Red, Brown
R2 | - 1.8k ohms - Brown, gray, black, brown
| Or Brown, Gray, Red
R3, R4 | - 220 ohms - Red, Red, brown
R5, R6 | - 330 ohms - Orange, Orange, brown
R7 | - 470 ohms - Yellow, violet, brown

Bend leads and insert.

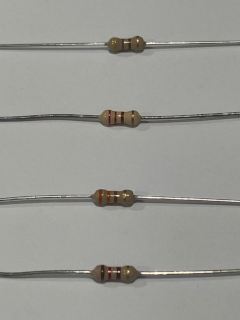
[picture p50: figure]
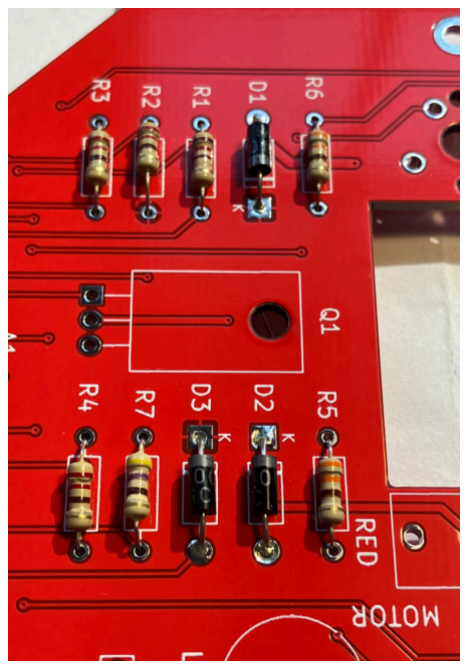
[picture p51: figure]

### 4. Q2 - 2N3904 BJT transistor

Install correct way around. Careful soldering to avoid bridges/shorts!

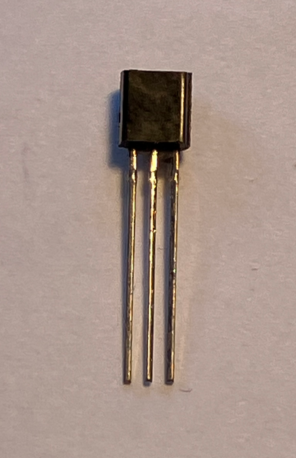
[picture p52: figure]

### 5. Q1 - RFP30N06 or IRF540 MOSFET transistor

Bend leads and install

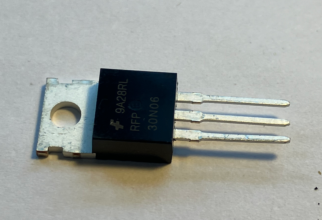
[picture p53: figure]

### 6. LS1 - Speaker

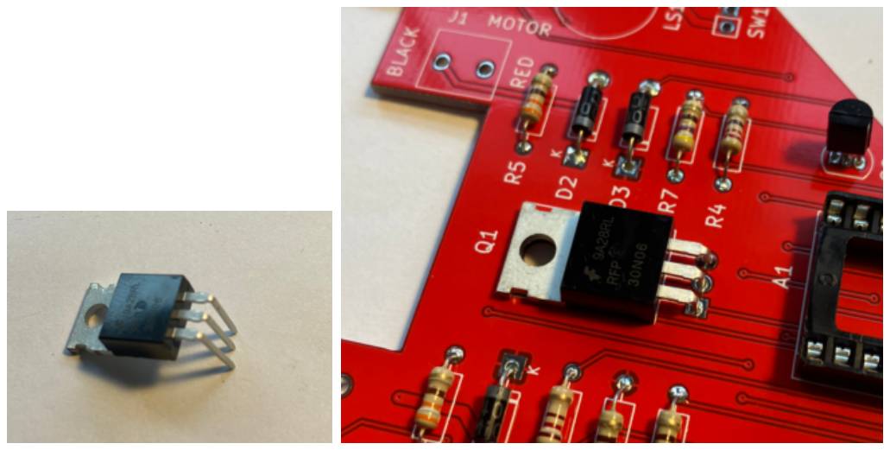
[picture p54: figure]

Install the right way around (see photo and “+” on the speaker)

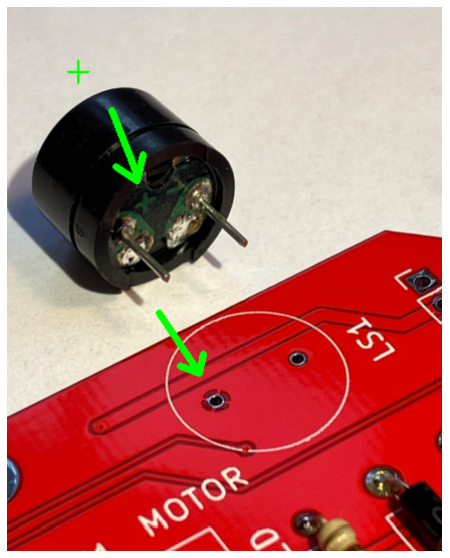
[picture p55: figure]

### 7. SW2 - push-button switch

Install from bottom side. Make sure it is flat against the PC board.

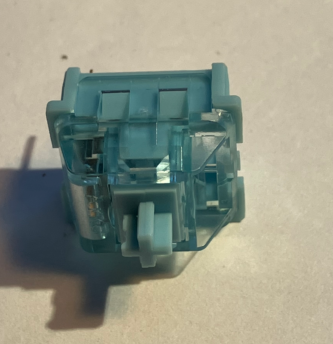
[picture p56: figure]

### 8. U1 - Optical sensor

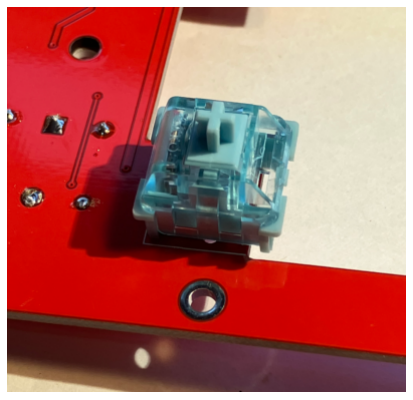
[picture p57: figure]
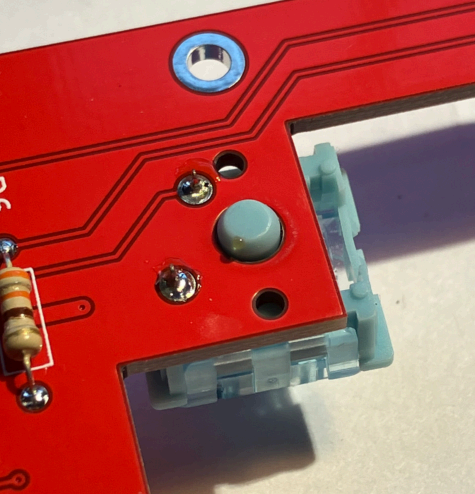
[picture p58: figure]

Install from bottom side. Plastic pins go in holes in PCB and it snaps into place. Be sure it is flat agains the PC board.

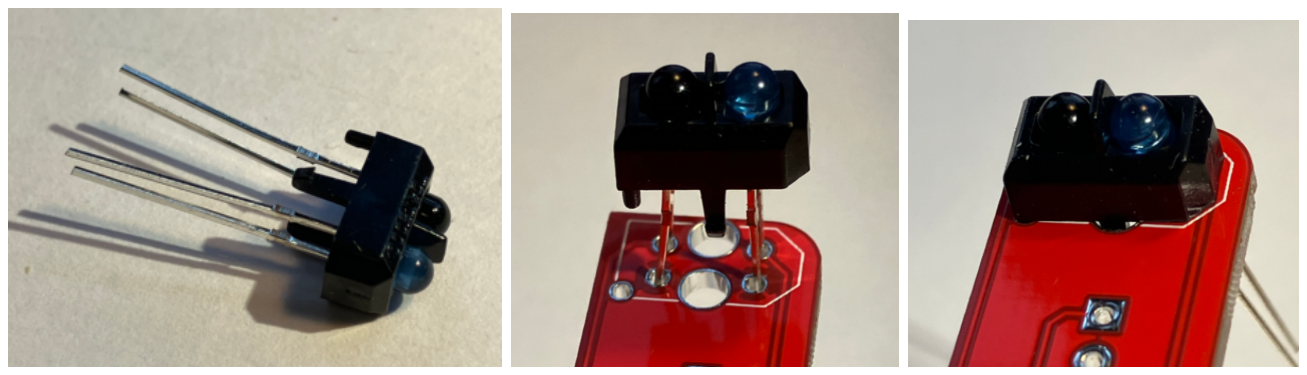
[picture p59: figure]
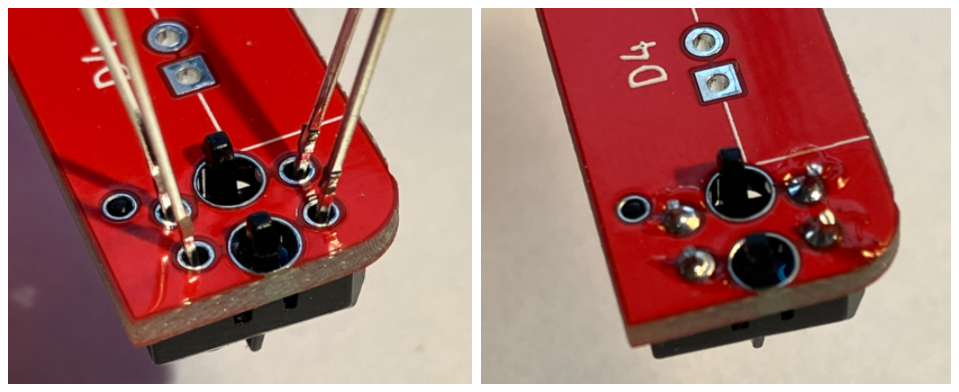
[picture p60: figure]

### 9. J1, J4 - screw terminals

Install from top side. Be sure the openings for the wires are towards the outside board edge. USE ONLY GREEN TERMINALS (the blue ones don’t work very well)

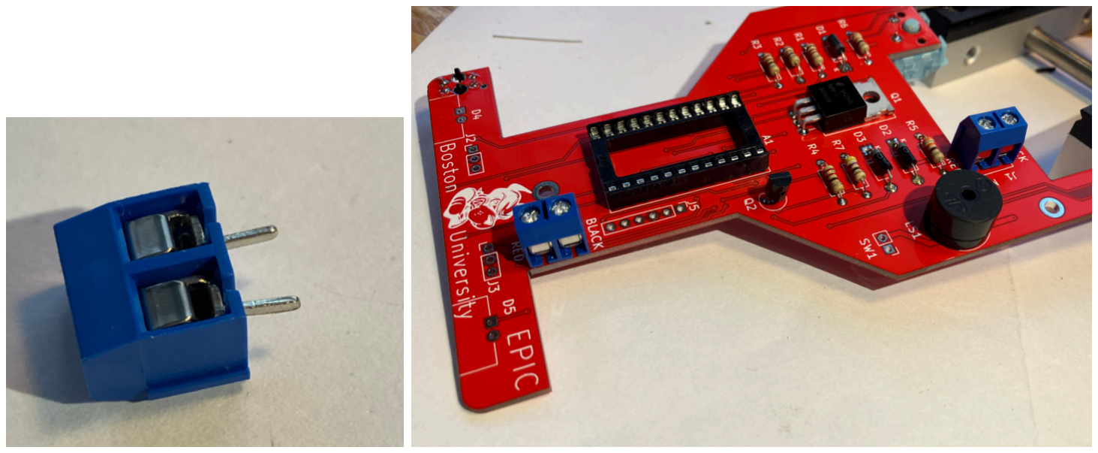
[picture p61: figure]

### 10. D6, D7 - RED LEDs (tail lights)

NOTE! One lead is longer than the other. This goes in the hole with the round silver pad Bend the leads at right angles as shown.

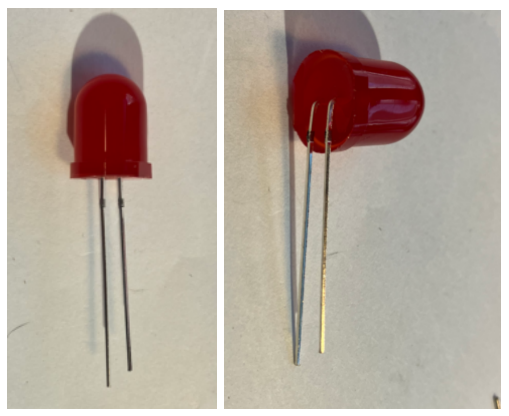
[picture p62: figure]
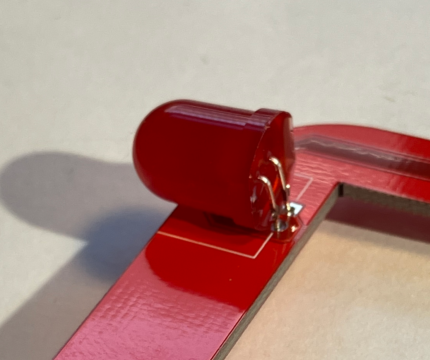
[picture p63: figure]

### 11. D4, D5 - WHITE LEDs (head lights)

Install the same way on the front of the car

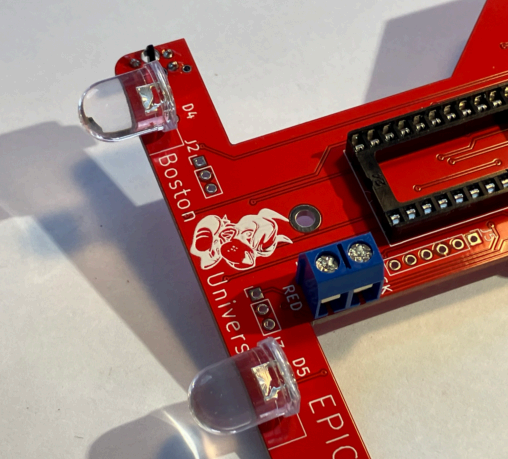
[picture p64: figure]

### 12. SW1 - Two-pin Header

Install with the short pins through the PC board and long pins sticking up

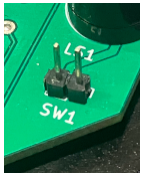
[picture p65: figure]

DONE! (with soldering)

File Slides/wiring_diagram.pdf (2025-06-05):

# Car Wiring Diagram

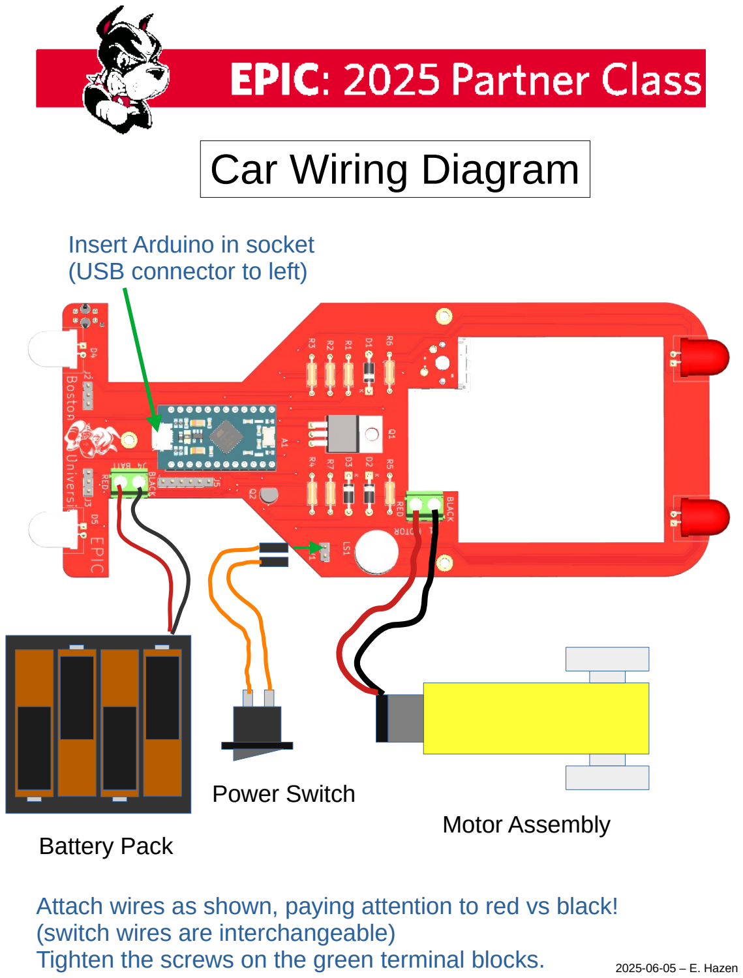
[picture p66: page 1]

Battery Pack

Power Switch
Motor Assembly

Insert Arduino in socket
(USB connector to left)

2025-06-05 – E. Hazen

Attach wires as shown, paying attention to red vs black! (switch wires are interchangeable)
Tighten the screws on the green terminal blocks.

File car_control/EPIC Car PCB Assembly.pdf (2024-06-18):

# PCB Assembly

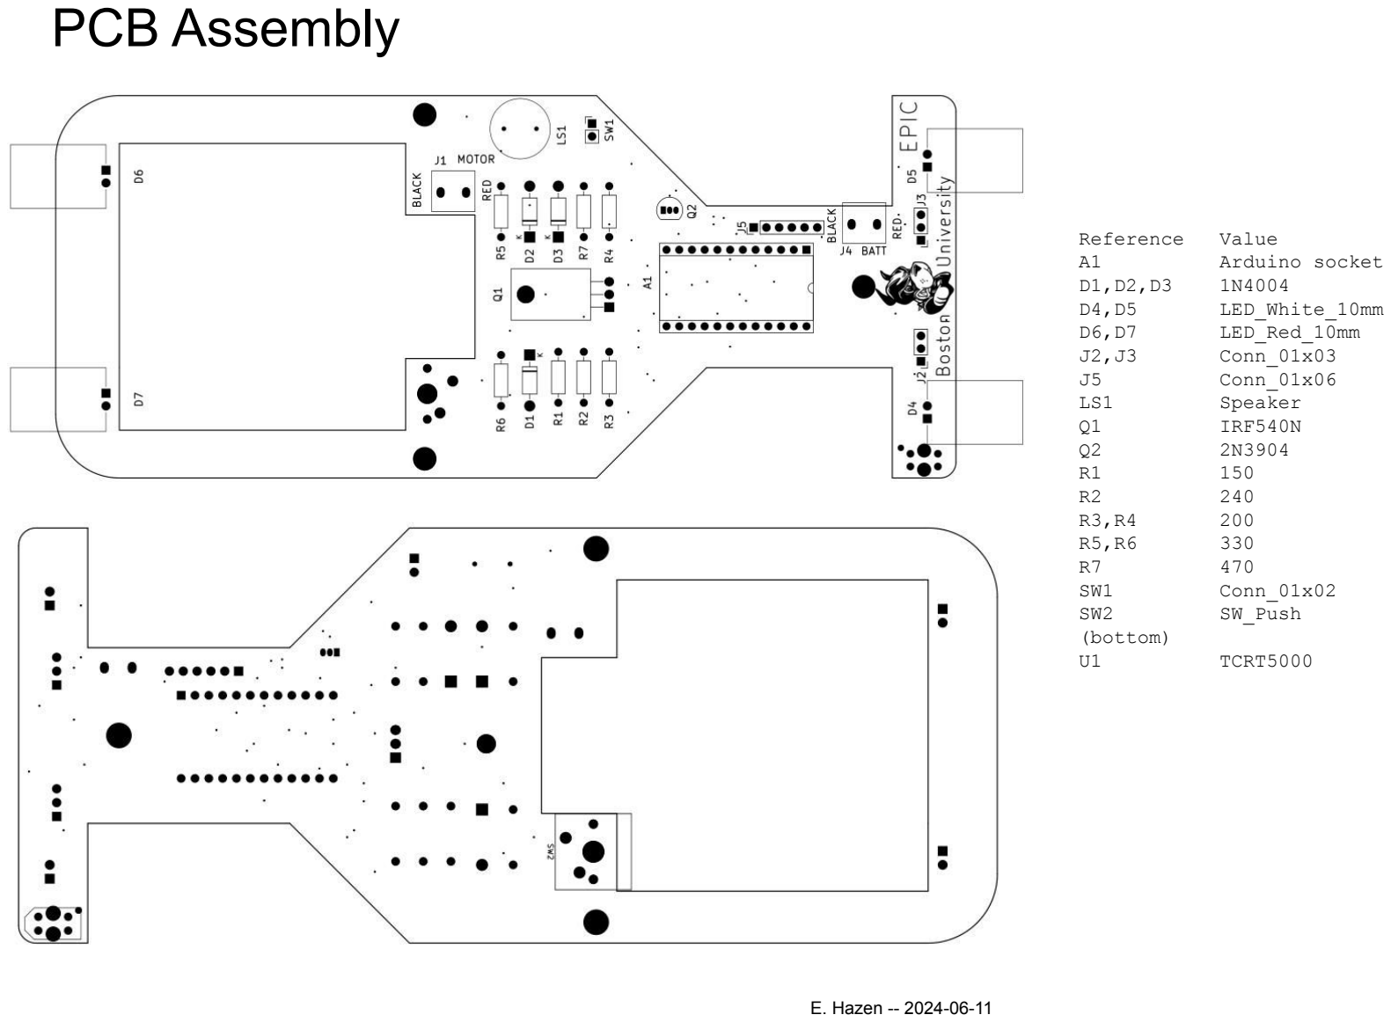
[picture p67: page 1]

Reference | Value
A1 | Arduino socket
D1,D2,D3 | 1N4004
D4,D5 | LED_White_10mm
D6,D7 | LED_Red_10mm
J2,J3 | Conn_01x03
J5 | Conn_01x06
LS1 | Speaker
Q1 | IRF540N
Q2 | 2N3904
R1 | 150
R2 | 240
R3,R4 | 200
R5,R6 | 330
R7 | 470
SW1 | Conn_01x02
SW2 | SW_Push
(bottom)
U1 | TCRT5000
E. Hazen -- 2024-06-11

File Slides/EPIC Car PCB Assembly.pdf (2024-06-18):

# PCB Assembly

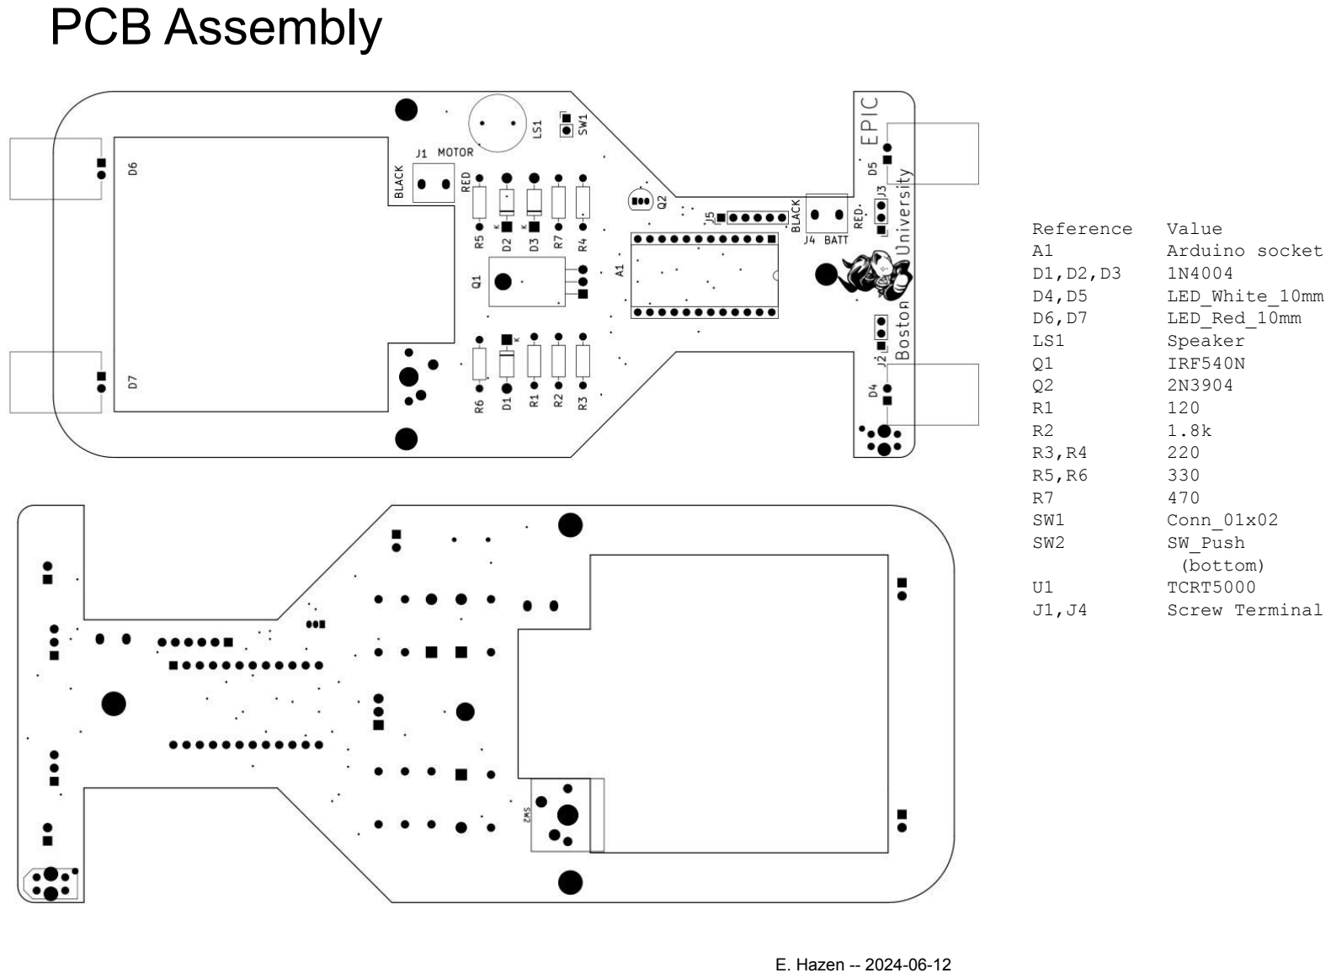
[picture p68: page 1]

Reference | Value
A1 | Arduino socket
D1,D2,D3 | 1N4004
D4,D5 | LED_White_10mm
D6,D7 | LED_Red_10mm
LS1 | Speaker
Q1 | IRF540N
Q2 | 2N3904
R1 | 120
R2 | 1.8k
R3,R4 | 220
R5,R6 | 330
R7 | 470
SW1 | Conn_01x02
SW2 | SW_Push
| (bottom)
U1 | TCRT5000
J1,J4 | Screw Terminal
E. Hazen -- 2024-06-12

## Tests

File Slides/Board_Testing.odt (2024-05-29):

# Car PCB Testing Rev 5/29/24

Test 1 (basic operation)

1. Install a programmed Arduino (white sticker on the MCU chip) Be sure it has the USB connector pointing forward
2. Connect Battery, switch, motor according to wiring diagram
3. Turn on the switch. Three LEDs should come on (binary firmware version, currently 7) Then, all the LEDs should flash, the speaker should beep and the motor should run briefly
4. Press the button on the bottom. The motor should start running

Test 2 (rotation sensor)

1. Switch off
2. Press button, hold down while turning on continue to hold button for about 3s and release
3. You should hear a series of beeps and a “chirp”
4. Wave your finger or another object in front of the optical sensor (right front on the bottom) You should hear a series of short beeps.

If anything doesn’t work as expected, make a note of the board number.

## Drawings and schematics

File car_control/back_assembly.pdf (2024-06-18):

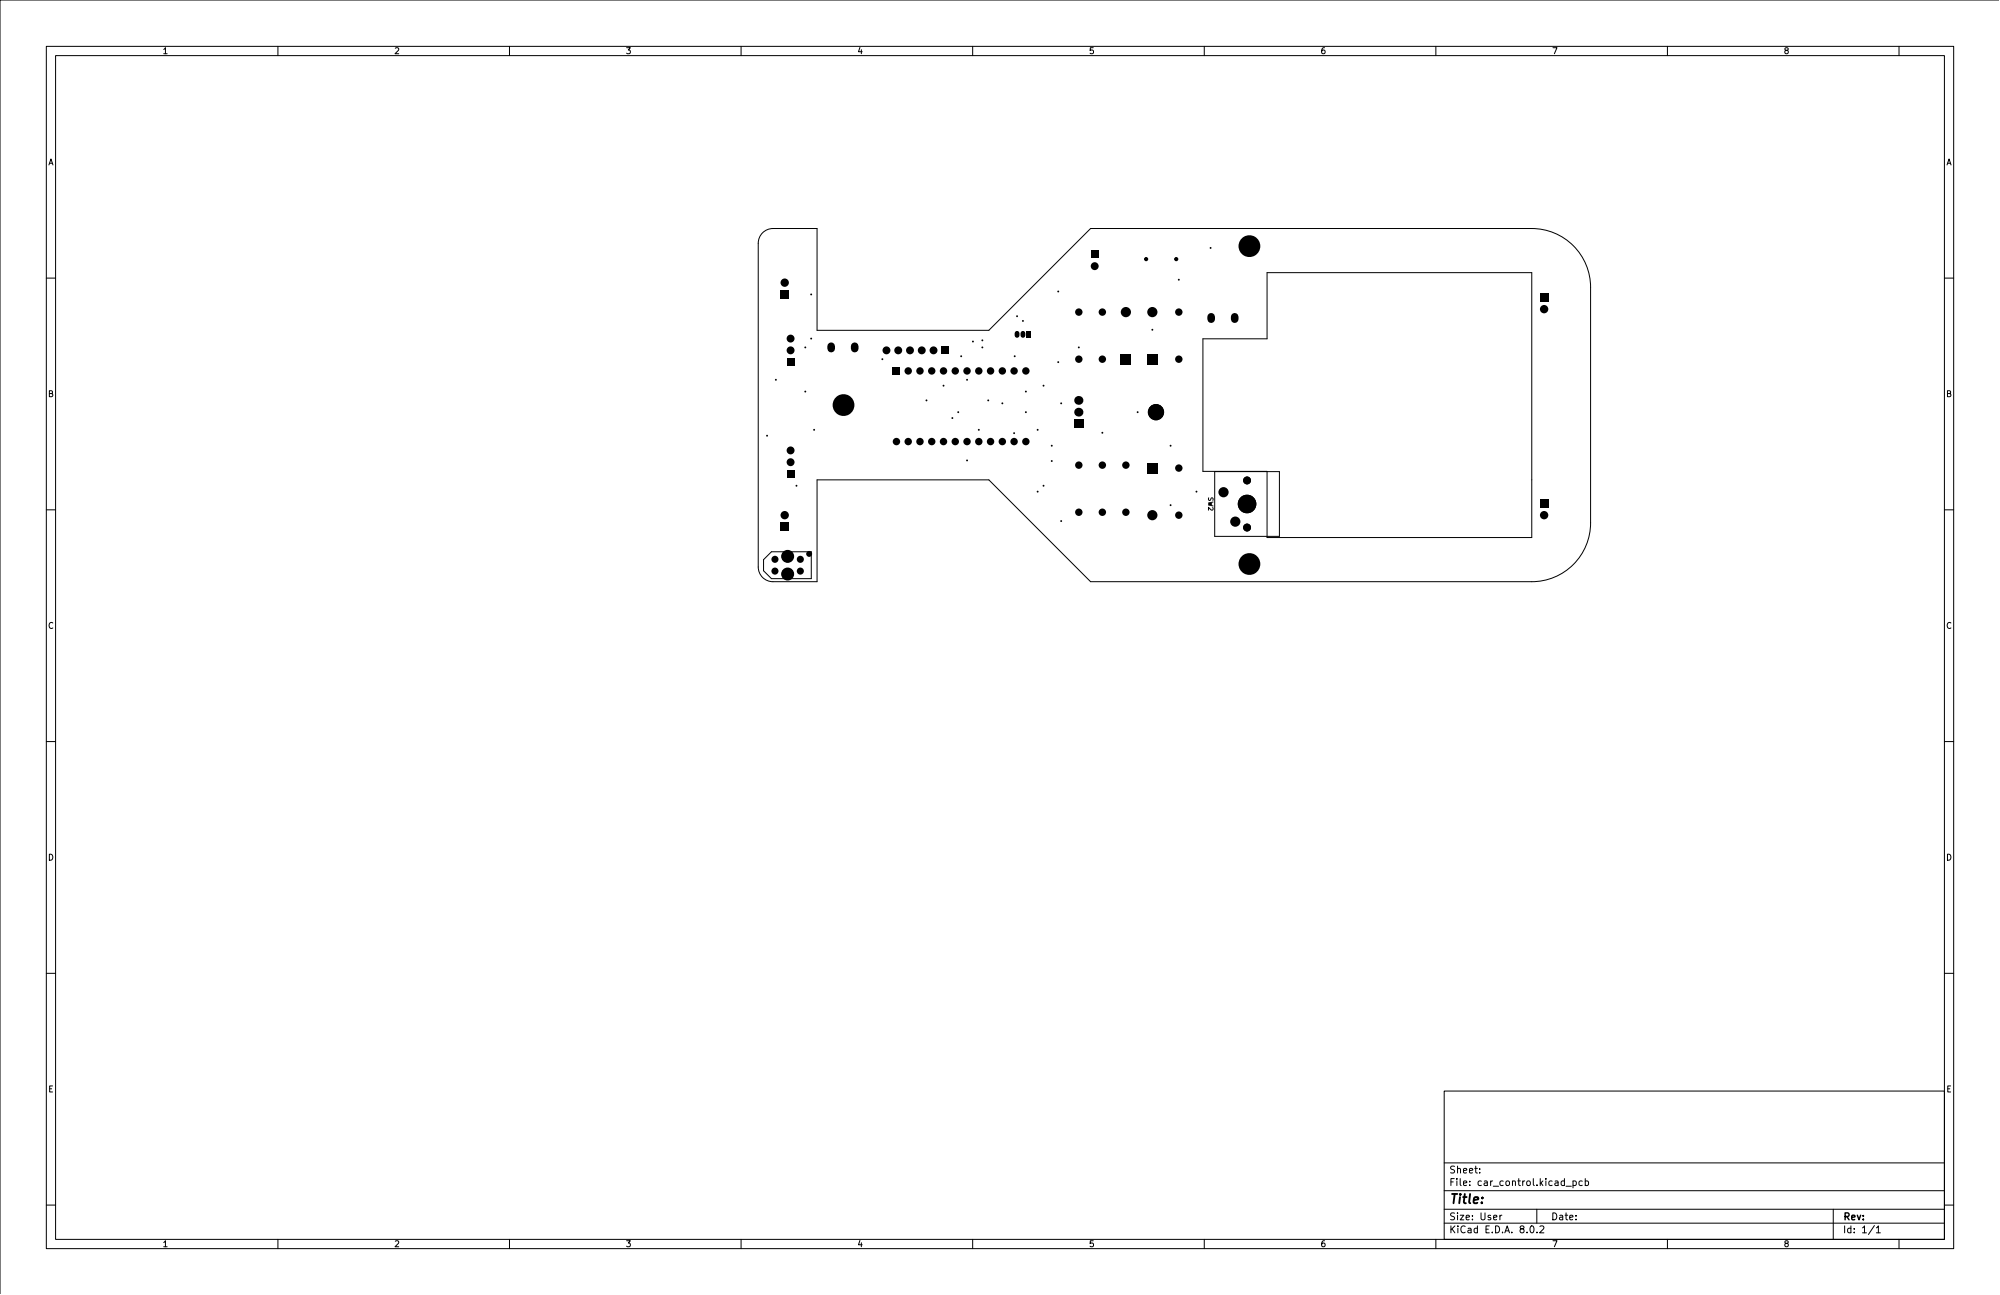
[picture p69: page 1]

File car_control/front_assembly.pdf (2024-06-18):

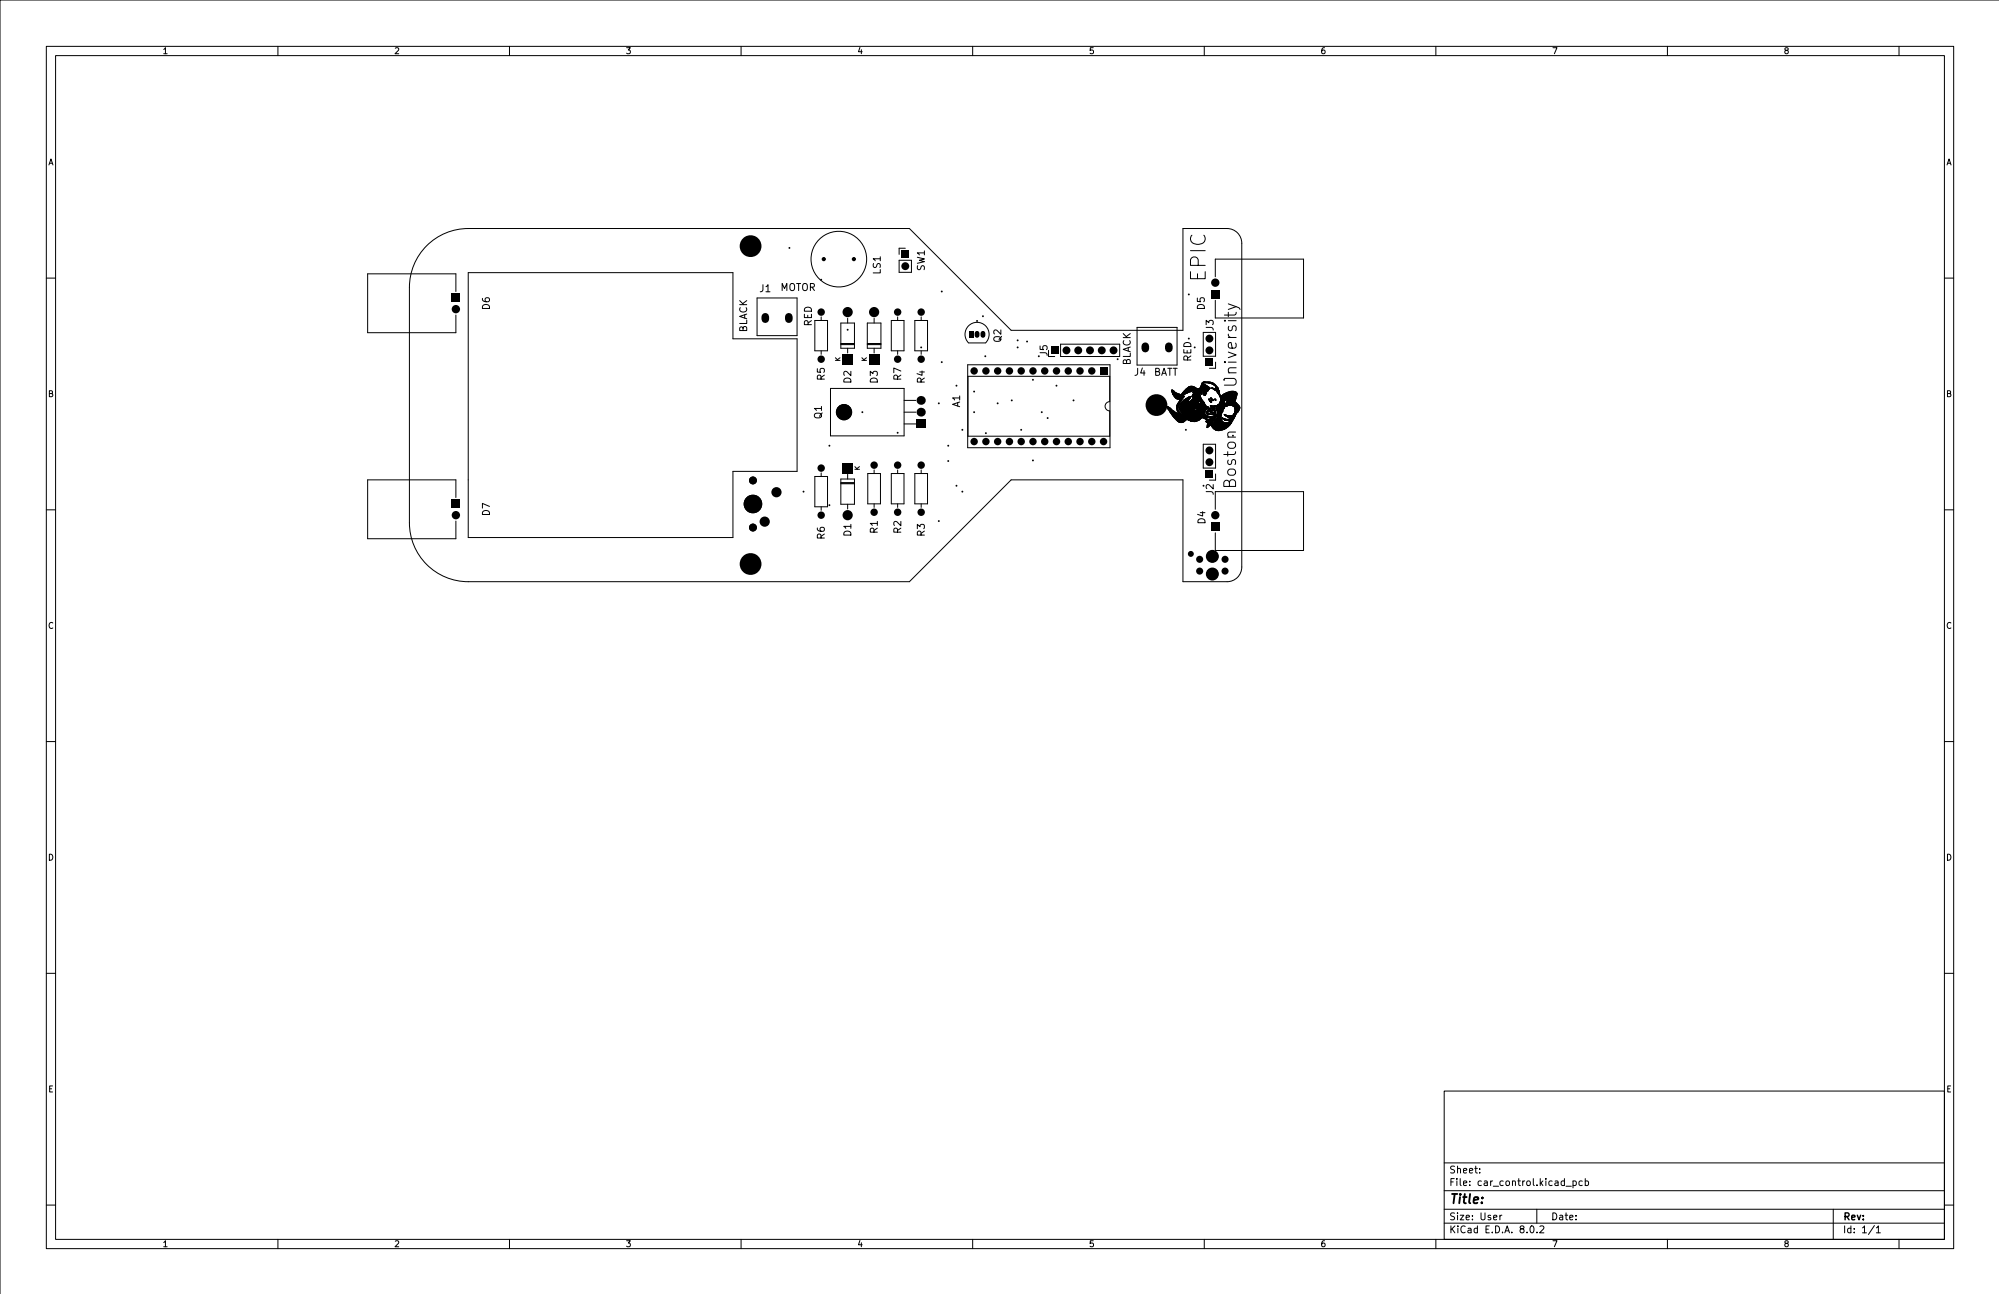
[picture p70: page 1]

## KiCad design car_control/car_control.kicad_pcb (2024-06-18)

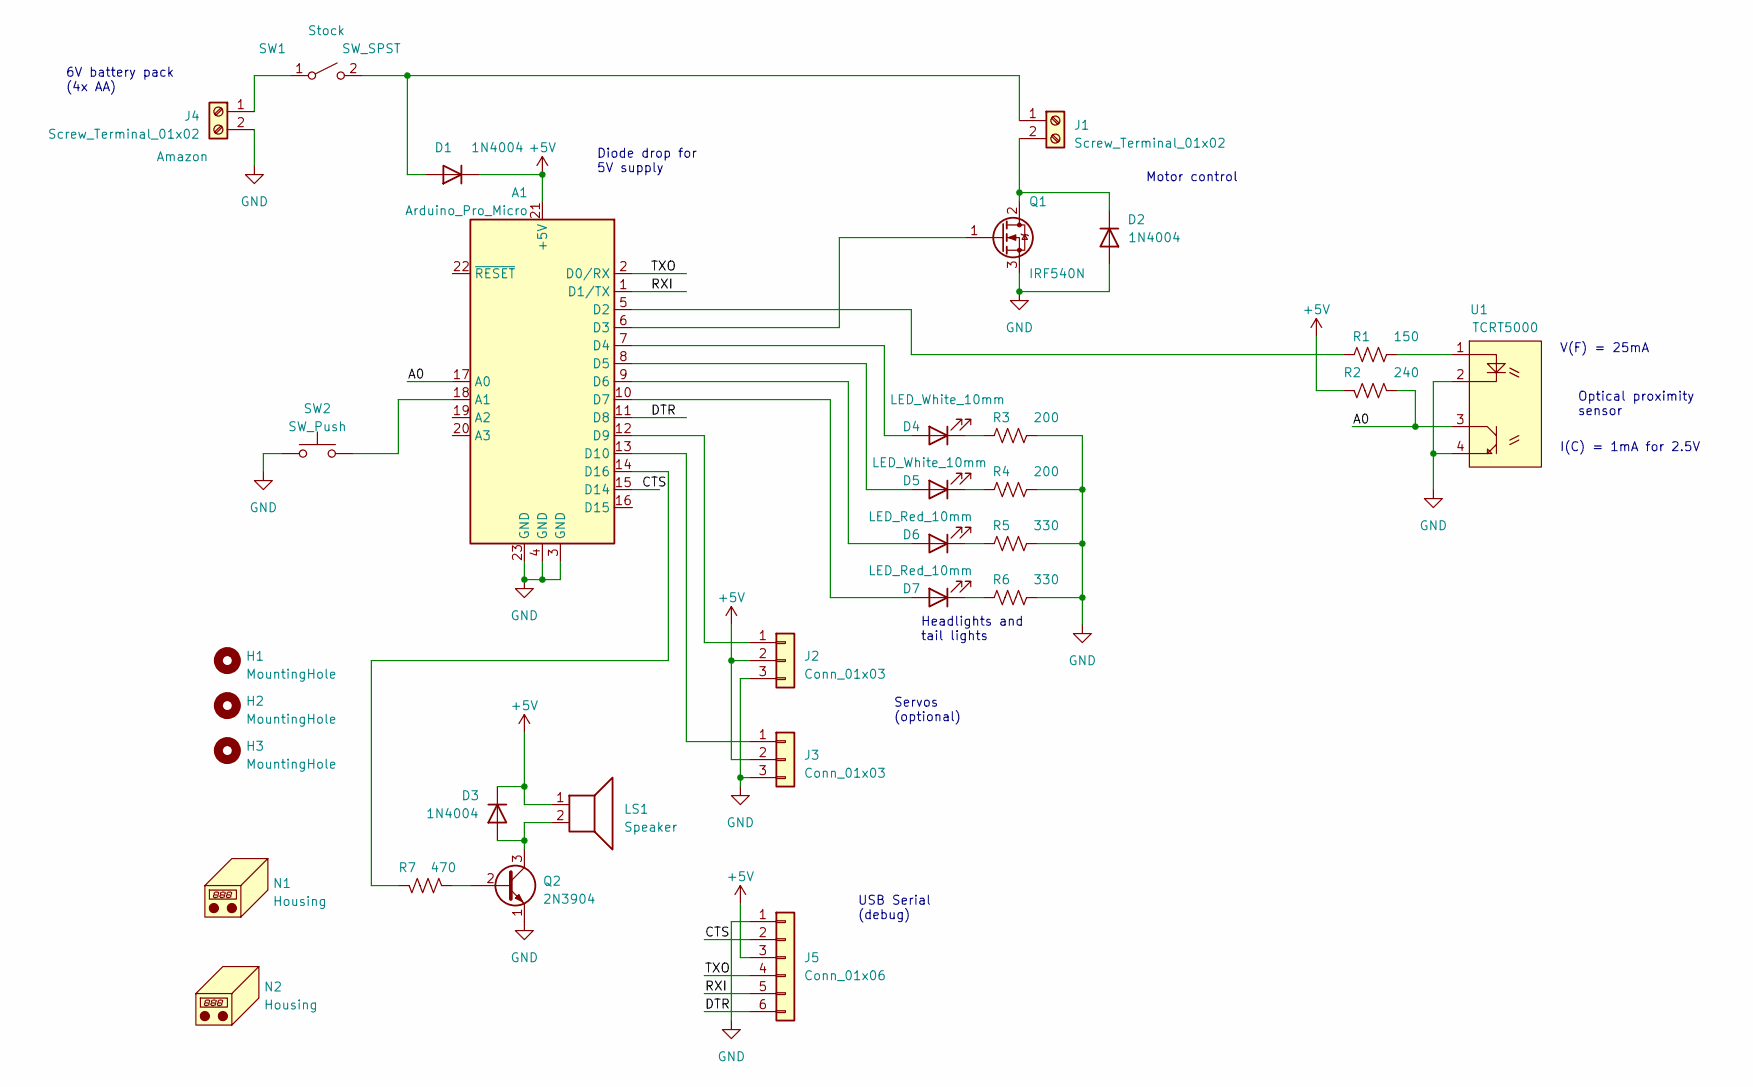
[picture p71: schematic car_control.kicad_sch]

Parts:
A1: Arduino_Pro_Micro; pro_micro_socket
D1, D2, D3: 1N4004; D_DO-41_SOD81_P10.16mm_Horizontal
D4, D5: LED_White_10mm; LED_D10.0mm_white
D6, D7: LED_Red_10mm; LED_D10.0mm_red
H1, H2, H3: MountingHole; MountingHole_2.7mm_M2.5_DIN965_Pad
J1, J4: Screw_Terminal_01x02; Wuerth_WR-WTB_64800211622_1x02_P1.50mm_Vertical
J2, J3: Conn_01x03; PinHeader_1x03_P2.54mm_Vertical
J5: Conn_01x06; PinHeader_1x06_P2.54mm_Vertical
LS1: Speaker; speaker_d12mm_h8.5_p6.5
N1: Housing; rhett_logo
N2: Housing; car_as
Q1: IRF540N; TO-220-3_Horizontal_TabDown
Q2: 2N3904; TO-92_Inline
R1: 150; R_Axial_DIN0207_L6.3mm_D2.5mm_P10.16mm_Horizontal
R2: 240; R_Axial_DIN0207_L6.3mm_D2.5mm_P10.16mm_Horizontal
R3, R4: 200; R_Axial_DIN0207_L6.3mm_D2.5mm_P10.16mm_Horizontal
R5, R6: 330; R_Axial_DIN0207_L6.3mm_D2.5mm_P10.16mm_Horizontal
R7: 470; R_Axial_DIN0207_L6.3mm_D2.5mm_P10.16mm_Horizontal
SW1: SW_SPST; PinHeader_1x02_P2.54mm_Vertical
SW2: SW_Push; SW_Cherry_MX_1.00u_PCB
U1: TCRT5000

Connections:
+5V: A1.21 (+5V), D1.1 (K), D3.1 (K), J2.2, J3.2, J5.3, LS1.1, R2.2
/A0: A1.17 (A0), R2.1, U1.3 (C)
/CTS: A1.15 (D14), J5.2
/DTR: A1.11 (D8), J5.6
/RXI: A1.1 (D1/TX), J5.5
/TXO: A1.2 (D0/RX), J5.4
GND: A1.3 (GND), A1.4 (GND), A1.23 (GND), D2.2 (A), J2.3, J3.3, J4.2, J5.1, Q1.3 (S), Q2.1 (E), R3.2, R4.2, R5.2, R6.2, SW2.1, U1.2 (C), U1.4 (E)
unnamed: A1.18 (A1), SW2.2
unnamed: A1.5 (D2), R1.1
unnamed: A1.6 (D3), Q1.1 (G)
unnamed: A1.7 (D4), D4.2 (A)
unnamed: A1.8 (D5), D5.2 (A)
unnamed: A1.9 (D6), D6.2 (A)
unnamed: A1.10 (D7), D7.2 (A)
unnamed: A1.12 (D9), J2.1
unnamed: A1.13 (D10), J3.1
unnamed: A1.14 (D16), R7.2
unnamed: D1.2 (A), J1.1, SW1.2 (B)
unnamed: D2.1 (K), J1.2, Q1.2 (D)
unnamed: D3.2 (A), LS1.2, Q2.3 (C)
unnamed: D4.1 (K), R3.1
unnamed: D5.1 (K), R4.1
unnamed: D6.1 (K), R5.1
unnamed: D7.1 (K), R6.1
unnamed: J4.1, SW1.1 (A)
unnamed: Q2.2 (B), R7.1
unnamed: R1.2, U1.1 (A)

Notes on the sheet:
6V battery pack (4x AA)
Diode drop for 5V supply
USB Serial (debug)
I(C) = 1mA for 2.5V
Optical proximity sensor
Servos (optional)
V(F) = 25mA
Motor control
Headlights and tail lights

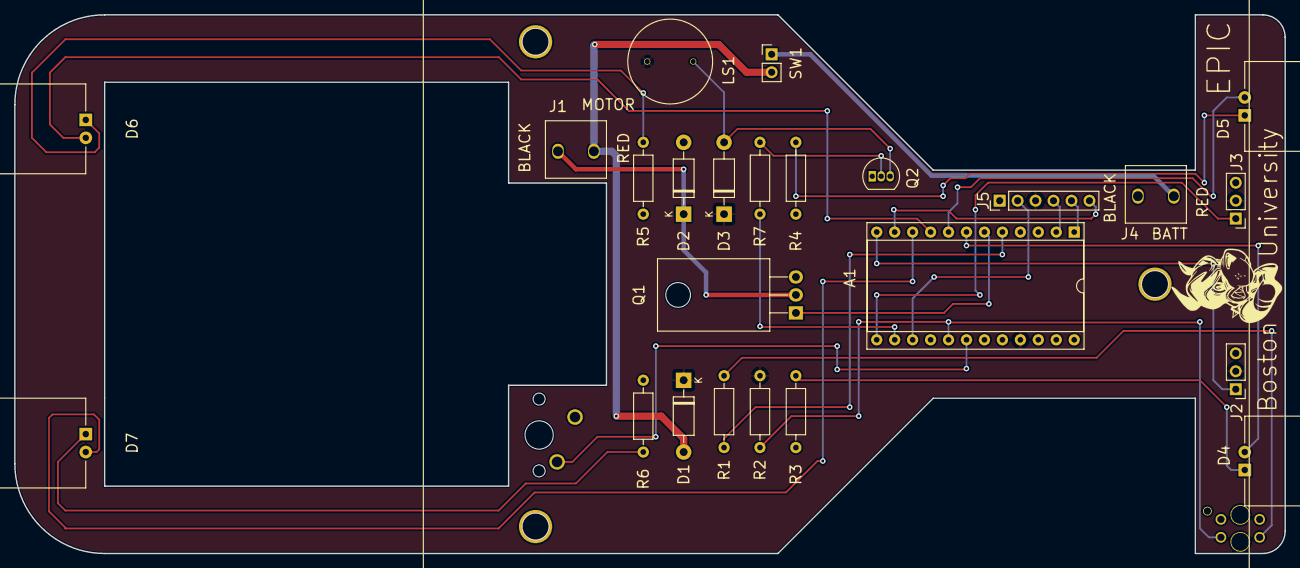
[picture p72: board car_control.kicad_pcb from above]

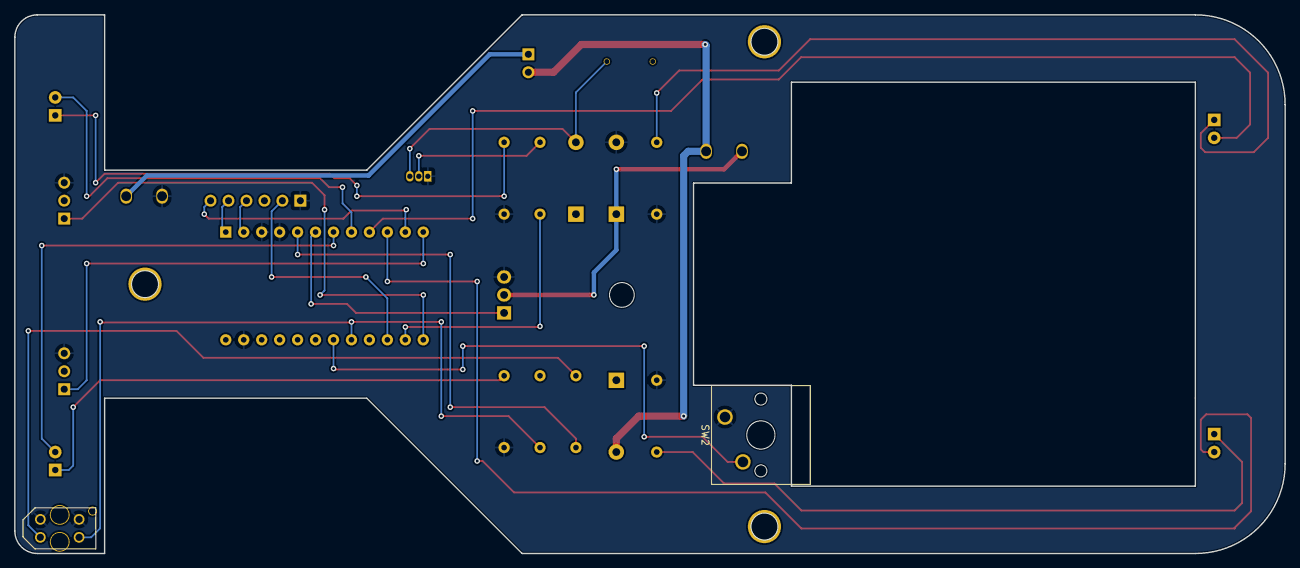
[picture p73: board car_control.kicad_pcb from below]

Board: 2 copper layers, 179.7 x 76.2 mm, 30 parts (2 on the bottom side), 27 nets.

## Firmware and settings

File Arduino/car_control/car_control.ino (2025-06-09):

//
// EPIC Car Control
//
// power-up reads distance set from EEPROM
//    long (error) beep means invalid setting (default to 5)
// Idle mode
//    short press - drive for programmed distance
//    long press - move to 10's set mode
// 10's set mode
//    short press: add 10 revs
//    long press: to 1's set mode
// 1's set mode
//    short press: add 1 revs
//    long press: save setting and exit to IDLE
//
// display value on LEDs in binary while setting
// if no short presses, just display and leave unchanged
// so 3 long presses just displays current value
//
// Mods:
// Rev 5 - used for June class
// Rev 6 - sensor threshold changed to 25 for a couple of cars
// Rev 7 - add sensor calibration code.
// Rev 8 - increase readSensor() range from 255 to 1023
// Rev 9 - debug/improved sensor EEPROM
// Rev 10 - fix bug in sensor EEPROM writing

// #define SERIAL_DEBUG

// please update me! (max is 15 on 4 LEDs)
#define REVISION 10



// #define DEBUG_STATE_ON_LEDS

#include <EEPROM.h>
#include "CarControl.hh"

CarControl car;			// create instance of car control

#ifdef SERIAL_DEBUG
void dump_eeprom( char *s) {
  // print EEPROM contents
  Serial.println(s);
  for( int i=0; i<8; i+=2) {
    Serial.print(i);
    Serial.print(" = ");
    Serial.println( eeprom_read_word(i));
  }
  // print car variables
  Serial.print("s_min: ");
  Serial.print(car.s_min);
  Serial.print(" s_max: ");
  Serial.print(car.s_max);
  Serial.print(" s_thr: ");
  Serial.println(car.s_thr);
}
#endif



// EEPROM offsets, all 16-bit values
// 0 = 0x5791
// 2 = rev counter
// 4 = sensor low value
// 6 = sensor high value
static const int EEP_MAGIC = 0;	// magic number 5791
static const int EEP_REVS = 2;	// revs counter (16 bits)
static const int EEP_SENSE_MIN = 4; // Sensor low value
static const int EEP_SENSE_MAX = 6; // Sensor high value

static const int EEP_MAGIC_VALUE = 0x5791;

// variables for the state machine which controls the car
// (these probably shoud be moved to the C++ class...)
static int state = S_IDLE;	// initial state
static int speed;		// speed 0-255
static int revs = 5;		// wheel revolutions to run

#define MAX_REV 100		// rev setting limit (default)

static bool rev_change;		// flag: changed revs

static int s_sum;		// sum for averaging

// programming blink rate in ticks (20ms tick, approximately)
#define PROG_FAST_BLINK 6
#define PROG_SLOW_BLINK 20
static uint8_t blinkt;

//
// display a binary value 0-15 on the LEDs
//
void binaryLights( int v) {
  digitalWrite( LED1_PIN, v & 1);
  digitalWrite( LED2_PIN, (v & 2) != 0);
  digitalWrite( LED3_PIN, (v & 4) != 0);
  digitalWrite( LED4_PIN, (v & 8) != 0);
}

//
// setup - most hardware setup already done in CarControl()
// read the EEPROM and set the rev counter
//
void setup() {
#ifdef SERIAL_DEBUG
  Serial.begin(115200);
  delay(5000);
  Serial.println("Debug mode");
#endif  
  car.beep( BEEP_LONG);			  // start with a long beep
  binaryLights( REVISION);		  // display version for 1 sec
  delay(1000);
  // chase around the LEDs to test them
  for( int i=0; i<4; i++) {
    car.setHeadLights( 0, 1);
    car.setTailLights( 0, 0);
    delay(100);  
    car.setHeadLights( 1, 0);
    car.setTailLights( 0, 0);
    delay(100);  
    car.setHeadLights( 0, 0);
    car.setTailLights( 0, 1);
    delay(100);  
    car.setHeadLights( 0, 0);
    car.setTailLights( 1, 0);
    delay(100);  
  }
#ifdef SERIAL_DEBUG
  dump_eeprom("startup");
#endif  
  // read stuff from non-volatile memory
  EEPROM.get( EEP_MAGIC, s_sum);
  if( s_sum == EEP_MAGIC_VALUE) { // EEPROM is valid
#ifdef SERIAL_DEBUG
    Serial.println("EE OK");
#endif    
    EEPROM.get( EEP_REVS, revs);
    EEPROM.get( EEP_SENSE_MIN, car.s_min);
    EEPROM.get( EEP_SENSE_MAX, car.s_max);
    car.beep( BEEP_SHORT);
  } else {			// EEPROM is invalid
#ifdef SERIAL_DEBUG
    Serial.println("EE bad");
#endif    
    revs = 5;
    car.s_min = 500;
    car.s_max = 1000;
    // write default values and beep quite a bit
    s_sum = EEP_MAGIC_VALUE;
    EEPROM.put( EEP_MAGIC, s_sum);
    EEPROM.put( EEP_REVS, revs);
    EEPROM.put( EEP_SENSE_MIN, car.s_min);
    EEPROM.put( EEP_SENSE_MAX, car.s_max);
    car.beep( BEEP_ERROR);
    car.beep( BEEP_ERROR);
  }
#ifdef SERIAL_DEBUG
  dump_eeprom("fixed");
#endif
  if( revs <= 0 || revs > MAX_REV) {			// if invalid, beep, set to 5
    car.beep(BEEP_ERROR);
    revs = 5;
  } else {						// make a happy sound
    for( int i=100; i<=400; i*=2) {
      tone( SPKR_PIN, i, 100);
      delay(100);
    }
    car.beep( BEEP_SHORT);
  }
  // twitch the motor
  car.setSpeed( 200);
  delay(100);
  car.setSpeed( 0);
  // if button pressed on power-up, go to diagnostic mode
  if( !car.readButton()) {
    //    state = S_DIAG;
    state = S_CALIB;    
    while( !car.readButton())				// wait for button release
      ;
    delay(100);
  } else {
    // start with taillights only on
    car.setHeadLights( 0, 0);
    car.setTailLights( 1, 1);
    
  }
}


//
// main loop - update the (Mealy) state machine every 20ms
//
void loop() {

#ifdef DEBUG_STATE_ON_LEDS
  // display FSM state on the LEDs for debugging
  binaryLights( state);
#endif  

  switch( state) {

  case S_IDLE:			// waiting for button press
    if( car.buttonPressed()) {	// short press, start running
      car.clearRevs();
      state = S_ACCEL;
      speed = 0;
    }
    if( car.buttonLong()) {	// long press, start programming
      car.beep(BEEP_HIGH);
      state = SP_TENS;
      blinkt = 0;
      rev_change = false;
    }
    break;

  case S_ACCEL:			// accelerating to speed
    car.setHeadLights( 0, 0);	// headlights off
    car.setTailLights( 0, 0);	// taillights off
    speed += ACCEL;
//    if( car.getRevs() >= revs) {
//      state = S_DECEL;		// hit the rev count - go decelerate
//    }
    if( speed >= 255) {		// max speed?
      speed = 255;
      state = S_RUN;		// go to running state
      car.clearRevs();
    }
    car.setSpeed( speed);
    break;

  case S_RUN:			// running - measure distance
    car.setHeadLights( 1, 1);	// headlights on
    car.setTailLights( 0, 0);	// taillights off
    if( car.getRevs() >= revs) {
      state = S_DECEL;		// hit the rev count - go decelerate
    }
    break;

  case S_DECEL:			// decelerating to stop
    car.setHeadLights( 0, 0);	// headlights off
    car.setTailLights( 1, 1);	// taillights on
    speed -= ACCEL;
    if( speed <= 0) {
      speed = 0;
      state = S_IDLE;		// stopped - go back to IDLE
    }
    car.setSpeed( speed);
    break;

  case SP_TENS:			// program tens of rotations
    // display tens on lights, slow blink
    if( blinkt == PROG_SLOW_BLINK)
      binaryLights( revs / 10);
    else if( blinkt == PROG_SLOW_BLINK*2) {
      blinkt = 0;
      binaryLights( 0);
    }
    if( car.buttonPressed()) {	// short press - increment count
      if( !rev_change) {
	revs = 0;		// changing the revs, zero first
	rev_change = true;
      }
      if( revs >= MAX_REV) {	// more than max?
	car.beep(BEEP_ERROR);	// yes, error beep
	state = S_IDLE;		// leave at error value
      } else {
	revs += 10;		// increment by 10
	car.beep(BEEP_SHORT);
      }
    } else if( car.buttonLong()) { // long press - go set ones
      car.beep(BEEP_LOW);
      state = SP_ONES;
      blinkt = 0;
    }
    break;

  case SP_ONES:			// program ones of rotations
    // display ones on lights, fast blink
    if( blinkt == PROG_FAST_BLINK)
      binaryLights( revs % 10);
    else if( blinkt == PROG_FAST_BLINK*2) {
      blinkt = 0;
      binaryLights( 0);
    }
    if( car.buttonPressed()) {
      if( !rev_change) {
	revs = 0;		// changing the revs, zero first
	rev_change = true;
      }
      if( revs >= MAX_REV) {
	car.beep(BEEP_ERROR);
	state = S_IDLE;
      } else {
	revs ++;
	car.beep(BEEP_SHORT);
      }
    } else if( car.buttonLong()) {
      car.beep(BEEP_LONG);
      state = SP_EXIT;
    }
    break;

  case SP_EXIT:			// program write data exit
    if( rev_change)
      EEPROM.put( EEP_REVS, revs);
    // start with taillights only on
    car.setHeadLights( 0, 0);
    car.setTailLights( 1, 1);
    state = S_IDLE;
    break;
    
  case S_DIAG:			// diagnostic display
    if( car.buttonPressed()) {
      state = S_DIAG1;
      // stop everything and get a sensor reading
      s_sum = 0;
      for( uint8_t i=0; i<SENS_AVG_COUNT; i++)
	s_sum += car.readSensor();
      s_sum /= SENS_AVG_COUNT;
      car.beep(BEEP_LONG);
    }
    break;

  case S_DIAG1:
    binaryLights( s_sum);
    if( car.buttonPressed()) {
      state = S_DIAG2;
      car.beep(BEEP_TICK);
    }
    break;

  case S_DIAG2:
    binaryLights( (s_sum >> 4));
    if( car.buttonPressed()) {
      state = S_DIAG;
      car.beep(BEEP_TICK);
    }      
    break;

  case S_CALIB:
#ifdef SERIAL_DEBUG
    Serial.println("calib");
#endif
    binaryLights( 15);
    car.s_min = 1023;
    car.s_max = 0;
    state = S_CALIB1;
    break;

  case S_CALIB1:
    s_sum = car.readSensor();
    if( s_sum > car.s_max)  {
      car.s_max = s_sum;
      car.beep( BEEP_TICK);
#ifdef SERIAL_DEBUG
      Serial.print("max ");
      Serial.println( car.s_max);
#endif      
    }
    if( s_sum < car.s_min) {
      car.s_min = s_sum;
      car.beep( BEEP_TOCK);
#ifdef SERIAL_DEBUG
      Serial.print("min ");
      Serial.println( car.s_min);
#endif      
    }
    if( car.buttonPressed()) {
      state = S_CALIB2;
      car.beep(BEEP_LONG);
    }
    break;

  case S_CALIB2:
#ifdef SERIAL_DEBUG
    Serial.print("cal: ");
    Serial.print(car.s_min);
    Serial.print("-");
    Serial.println(car.s_max);
#endif    
    EEPROM.update(EEP_SENSE_MIN, car.s_min & 0xff);
    EEPROM.update(EEP_SENSE_MIN+1, car.s_min >> 8);
    EEPROM.update(EEP_SENSE_MAX, car.s_max & 0xff);
    EEPROM.update(EEP_SENSE_MAX+1, car.s_max >> 8);
    car.beep(BEEP_SHORT);
    // start with taillights only on
    car.setHeadLights( 0, 0);
    car.setTailLights( 1, 1);
    state = S_IDLE;
    break;
  }

  // do this every 20ms or so
  car.updateRevs();		// update revolution sensor
  car.updateButton();		// update button press/debounce
  delay( TICK_MS);		// delay 20ms
  ++blinkt;			// increment counter for blinking LEDs
}

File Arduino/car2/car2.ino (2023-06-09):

/*
 * EPIC model car
 * Wait for pushbutton
 * run for configured distance
 * stop
 */

#include <ezBuzzer.h>

// pins
#define LED1_PIN 4
#define LED2_PIN 5
#define LED3_PIN 6
#define LED4_PIN 7
#define MOTOR_PIN 3
#define SENS_LED_PIN 2
#define SENS_INPUT_PIN A0
#define SERVO1_PIN 9
#define SERVO2_PIN 10
#define SPKR_PIN 16
#define BUTTON_PIN A1

// states
#define S_IDLE 0
#define S_ACCEL 1
#define S_RUN 2
#define S_DECEL 3

// other constants
#define TARGET_DISTANCE 10   // desired distance in revolutions
#define ACCEL 5   // acceleration in speed units per tick
#define SENSOR_THRESHOLD 900  // proximity sensor threshold

// variables
uint8_t state;  // current state from above
int m_speed;  // current motor speed
int distance;   // distance since start

// initialize buzzer library
ezBuzzer buzzer( SPKR_PIN);

// the setup function runs once when you press reset or power the board
void setup() {
  // Declare output pins
  pinMode(LED1_PIN, OUTPUT);
  pinMode(LED2_PIN, OUTPUT);
  pinMode(LED3_PIN, OUTPUT);
  pinMode(LED4_PIN, OUTPUT);
  pinMode(SPKR_PIN, OUTPUT);
  pinMode(MOTOR_PIN, OUTPUT);
  pinMode(SENS_LED_PIN, OUTPUT);

  // button is an input with pullup
  pinMode(BUTTON_PIN, INPUT_PULLUP);

  // start with motor and LEDs off
  digitalWrite( MOTOR_PIN, LOW);
  digitalWrite( LED1_PIN, LOW);
  digitalWrite( LED2_PIN, LOW);
  digitalWrite( LED3_PIN, LOW);
  digitalWrite( LED4_PIN, LOW);
  digitalWrite( SENS_LED_PIN, LOW);
  
  state = S_IDLE;

  buzzer.beep(500);
}



// the loop function runs over and over again forever
void loop() {

   
  switch( state) {
    
    case S_IDLE:   // idle state, waiting for button press
      // wait for button
      if( digitalRead( BUTTON_PIN) == LOW) {
        state = S_ACCEL;
        m_speed = 0;
        digitalWrite( LED1_PIN, HIGH);      // light one of the headlights
        digitalWrite( SENS_LED_PIN, HIGH);  // activate the sensor
        buzzer.beep(50);
      }
      break;
      
    case S_ACCEL:  // accelerating
      m_speed += ACCEL;
      if( m_speed > 255) {
        m_speed = 255;
        state = S_RUN;
        digitalWrite( LED2_PIN, HIGH);
      }
      break;
      
    case S_RUN:   // running
      // check distance
      if( analogRead( SENS_INPUT_PIN) < SENSOR_THRESHOLD) {
        digitalWrite( LED4_PIN, HIGH);
        ++distance;
        buzzer.beep(10);
        if( distance > TARGET_DISTANCE) {
          state = S_DECEL;
        }
      } else
        digitalWrite( LED4_PIN, LOW);
      break;

    case S_DECEL:  // slowing down
      m_speed -= ACCEL;
      if( m_speed <= 0) {              // we're stopped
        m_speed = 0;
        state = S_IDLE;
        distance = 0;
        // turn off all the LEDs
        digitalWrite( LED1_PIN, LOW);
        digitalWrite( LED2_PIN, LOW);
        digitalWrite( LED3_PIN, LOW);
        digitalWrite( LED4_PIN, LOW);
        // turn of the distance sensor to save power
        digitalWrite( SENS_LED_PIN, LOW);
        buzzer.beep(500);
      }
      break;

    default:
      state = S_IDLE;      
  }
  if( state != S_IDLE)
    analogWrite( MOTOR_PIN, m_speed);
 
  delay(50);  // run the loop at about 20Hz
}

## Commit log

2023-05-26 Initial schematic
    [car_control.kicad_pcb, car_control.kicad_sch]
2023-05-26 initial schematic done?
    [car_control.kicad_pcb, car_control.kicad_sch]
2023-05-26 working on mechanics
    [car_control.kicad_pcb, car_control.kicad_sch]
2023-05-27 working on PCB mechanics
    [Pro_Micro.stl, TCRT5000.stl, TCRT5000.stp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]
2023-05-28 New board outline with wings
    [board.dxf, car_control.kicad_pcb, car_control.kicad_sch]
2023-05-28 candidate placement
    [car_control.kicad_pcb, car_control.kicad_sch]
2023-05-29 first version done?
    [board2.dxf, car_as_footprint.scad, car_as_footprint.stl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]
2023-05-29 version 2 with tail
    [car_control.kicad_pcb]
2023-05-30 Add USB serial connector
    [car_control.kicad_pcb, car_control.kicad_sch]
2023-05-30 Right angle 10mm headlights/tail lights
    [car_control.kicad_pcb, car_control.kicad_sch, led_10mm.scad]
2023-05-30 playing with board outlines
    [board3.dxf]
2023-05-31 update board outline
    [chassis_only.dxf, modified_chassis.dxf]
2023-05-31 Updated PCB outline (PCB3) and adjust battery mount holes
    [chassis_only.dxf, modified_chassis.dxf]
2023-05-31 New board outline, LEDs need fixing
    [car_control.kicad_pcb, led_10mm.scad]
2023-05-31 add cherry switch, change pwr sw to header, reroute
    [#modified_chassis.dxf, car_control.kicad_pcb, car_control.kicad_sch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]
2023-05-31 Rev 1 as built
    [car_control-B_Cu.gbr, car_control-B_Mask.gbr, car_control-B_Silkscreen.gbr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]
2023-06-05 chassis revision
    [chassis_revision.dxf]
2023-06-15 add build list
    [car_control_build.ods]
2023-06-19 LED display of values
2023-06-19 sensor test
2023-06-20 update initial power-up sequence
2023-06-21 working on setting LED blink
2023-06-21 Fix spurious blinking. V5 release candidate
    [car_control.ino]
2023-06-30 V7 sensor code not yet working
2023-06-30 Rev 7 with sensor calibration
2024-06-04 V8 software with sensor range increase to 1023
2025-02-14 starting on steering
    [steer.scad]
2025-04-24 working on steering
    [steer.scad]
2025-04-25 initial pass at steering parts
    [steer.scad]
2025-05-29 Version 9 with EEPROM sensor limits fixed
    [car_control.kicad_sch]
2025-06-05 update doco for 2025
    [car_control.kicad_sch]
2025-06-06 Rev 10 firmware to fix last (?) EEPROM bug
    [bracket.3mf, chassis.3mf, crossbar.3mf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]
